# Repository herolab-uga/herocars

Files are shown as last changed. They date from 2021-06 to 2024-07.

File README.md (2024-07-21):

# HeRoCars Project
This repo consists of details and open-sourced codes and materials of the HeRoCars - a Robotics Learning Technology developed at the Heterogeneous Robotics Lab of the University of Georgia. HeRoCars is a simulator-hardware integrative framework consisting of a game-inspired Unity-based Simulator module and a low-cost hardware module of robotized RC cars. 

Go to [Wiki page](https://github.com/herolab-uga/herocars/wiki) for more details.

# Welcome to the HeRoCars Project!
In this research, we focus on innovation in low-cost, open, intuitive learning and  education  methodologies  for  teaching  Robotics,  AI,  and  related  subjects. Here,  we  integrate  the  use  of  games  (e.g.,  Unity simulator  tool  for  testing robotic algorithms) and toys (RC vehicles converted to innovative robot plat-forms) in the proposed project. We first transform (robotize) a commercial RC car into a programmable car capable of sensing its environment through cameras and IR sensors and moving on a race track on its own using a microcomputer unit. Then, we develop a game-inspired Unity-based simulator for the car. Both the real car and the simulator are integrated in terms of the same educational modules that help teach and learn Robotics and AI concepts such as lane following and motor control.

## What will you learn from this project?
This project is jampacked with cool ideas, interesting technologies, and interactive activities for the user to take part in! One major thing you will learn about is AI! AI comes in many shapes and sizes and has a very broad range of possibilities. For this project, we will be discussing a very popular AI that is common in self-driving cars around the world! That AI model is a PID controller or a proportional–integral–derivative controller . A PID controller consist of 3 calculations that are then combined together to give you a smooth decision tree. Ever wonder why your air conditioner doesn't constantly make the temperature way colder the moment the temperature goes ever so slightly below the set temp? The reason is that many of them use a PID controller to help smooth out the temperature pattern and keep the temperature consistent without constantly overshooting the desired temperature. We will break the PID controller into 3 parts and describe what each element does, how it affects decisions, and how this can be applied into an RC car which we will make here shortly. But first, we must learn what an error is!

## Basics of PID and Error
[Click Here](https://github.com/herolab-uga/herocars/wiki/PID-Controller-and-Error) to learn about the PID controller and the concept of Error! You should fully read this before moving on for these two concepts are the main driving ideas behind this project.

## RC Car Hardware Assembly and Software Installation
There are two guides for building the car and installing the software. It is recommended that you start with the hardware portion and then do the software installation. 

[Click Here](https://github.com/herolab-uga/herocars/wiki/Hardware-Assembly-Guide) for the hardware assembly guide.

[Click Here](https://github.com/herolab-uga/herocars/wiki/Software-Assembly-Guide) for the software installation guide.

## RC Car Simulation in Unity Game Environment
[Click Here](https://github.com/herolab-uga/herocars/wiki/Simulator-Instructions) for instructions, information and a link to download our RC car simulator software designed with the Unity game engine!

## RC Car Interface Tool to Control and Test the Hardware Car (Integrated with the Simulation Software)
[Click Here](https://github.com/herolab-uga/herocars/wiki/RC-Car-Interface) for instructions on how to use the Unity-based simulator software to interface and control the actual RC car

## Final Robotized RC Car After Assembly
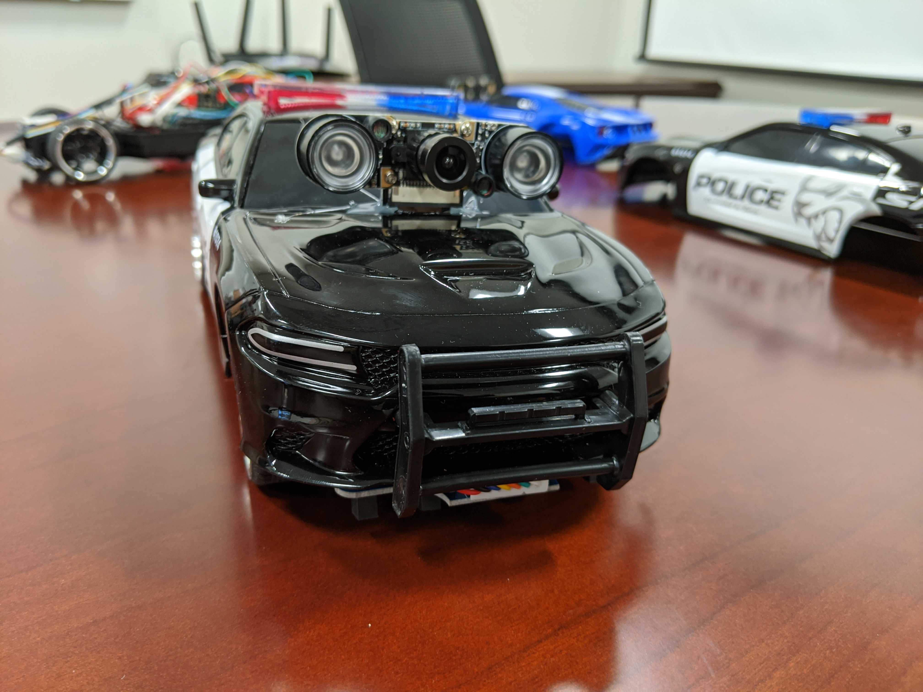
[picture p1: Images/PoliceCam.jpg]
RC Car

## Demo of the Robotized RC Car Driving Around the Track
RC Car Driving Around the Track
## Demo of the Simulator Software
Demo Vid

## Core contributors

* **Anderson Molter** - (https://github.com/andersonmolter1)

* **Sanjay Sarma O.V** - (https://github.com/sanjayovs)

* PI: Prof. Ramviyas Parasuraman - HeRoLab,  UGA - (http://hero.uga.edu)

* Co-PI: Prof. Prashant Doshi - THINC Lab, UGA - (http://thinc.cs.uga.edu)

## Heterogeneous Robotics (HeRoLab)

This project is a part of a Learning Technology Grant (LTG) project at the Heterogeneous Robotics Research Lab (HeRoLab) of the University of Georgia.

Please contact hero at uga . edu for any queries

https://hero.uga.edu/

<p align="center">

</p>

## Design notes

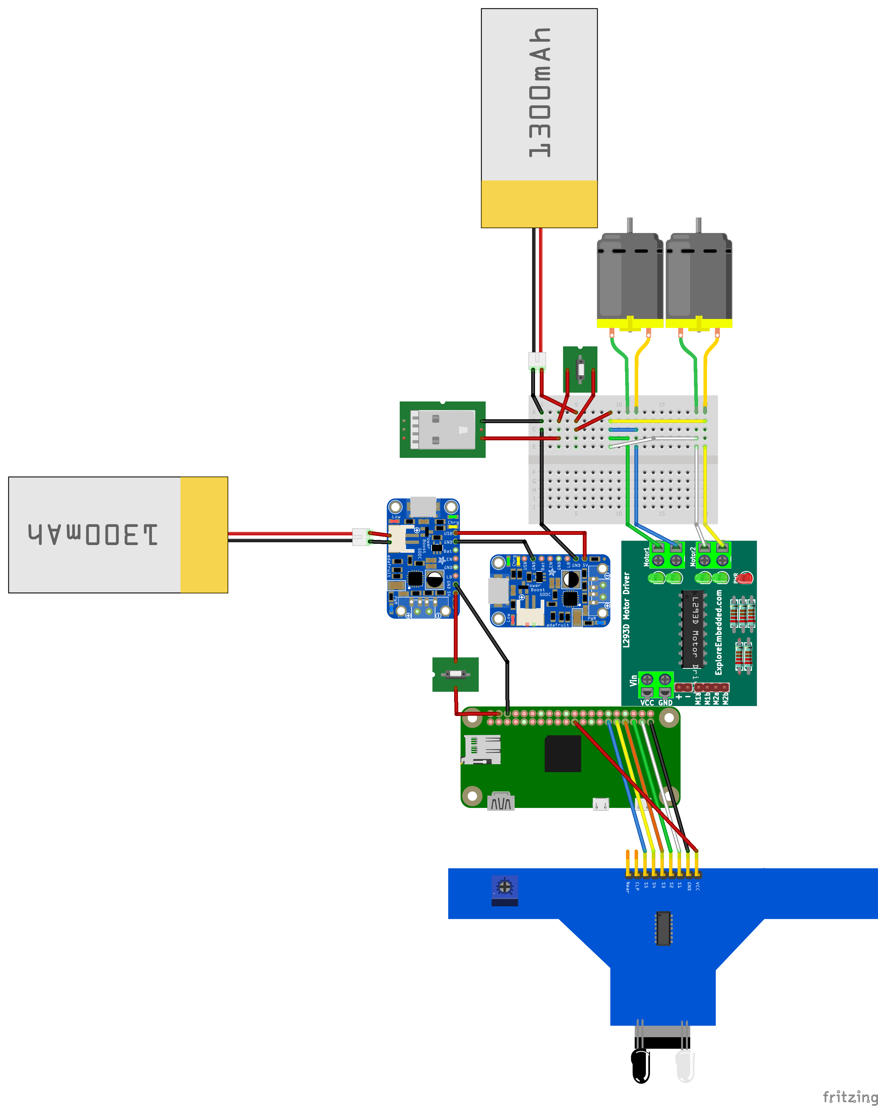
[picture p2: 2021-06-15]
Images/Design_1_bb.png

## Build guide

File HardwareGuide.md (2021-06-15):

# Hardware Assembly Guide
## Bill of Materials
| Component | Price | Quantity | Description | Part Number/SKU | Link to Buy |
| --- | --- | --- |--- | --- | --- |
| SparkFun Autophat | $29.95 | 1 | MotorDriver and IMU sensor | ROB-16328 | [Link to Buy](https://www.sparkfun.com/products/16328)
| Raspberry Pi Zero Wireless WH (Pre-Soldered Header)| $14.95 | 1 | Small computer for internal motor control and user connectivity | 1052 | [Link to Buy](https://www.pishop.us/product/raspberry-pi-zero-wireless-wh-pre-soldered-header/)
| Tracker Sensor Module 5-ch ITR20001/T | $9.99 | 1 | IR sensor array used to track line. Comes with 5 IR sensors pre-soldered.| ITR20001/T | [Link to Buy](https://www.amazon.com/Waveshare-Tracker-Sensor-ITR20001-Infrared/dp/B01MTPEKDC)
| Jada Toys Hyperchargers | $48.20 | 1 | RC Car in which the components will be installed. | 31122 | [Link to Buy](https://www.amazon.com/Jada-Hyperchargers-Chase-Control-Vehicle/dp/B07TYGQDSH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)
| Camera Module for Raspberry PI | $13.99 | 1 | Camera to sit on hood of car and stream video to user. | B07JXZ93SK | [Link to Buy](https://www.amazon.com/Dorhea-Raspberry-Camera-Adjustable-Focus-Infrared/dp/B07JXZ93SK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)
| JDB Ultra-Slim 5V/2.1A 5000mAh Power Bank | $9.99 | 1 | Power bank for all components of car. | 5K01 | [Link to Buy](https://www.amazon.com/gp/product/B07DQG75MZ/ref=ppx_yo_dt_b_search_asin_title?ie=UTF8&psc=1)
| Short USB C Cable | $6.99 | 1 | Cable to connect the Autophat to the battery bank via USB-C to USB-A.| 2724571560050 |  [Link to Buy](https://www.amazon.com/gp/product/B08LL1SVZD/ref=ppx_yo_dt_b_search_asin_title?ie=UTF8&psc=1)

## Hardware
Much work has done to simplify this process of assembling the car itself. But to start this process, you must first have the car. For this project, we are using a Jada R/C Hypercharger RC car. The pack will come with a police car and red race car. Both cars work the same way, however, the police car has a little more space inside so we will start with that one. However, all elements of this tutorial apply to both.

The Fritzing diagram below lays out the electrical diagram the car will follow. If you are confused by an instruction or image, it is HIGHLY recommended to come back to this guide.

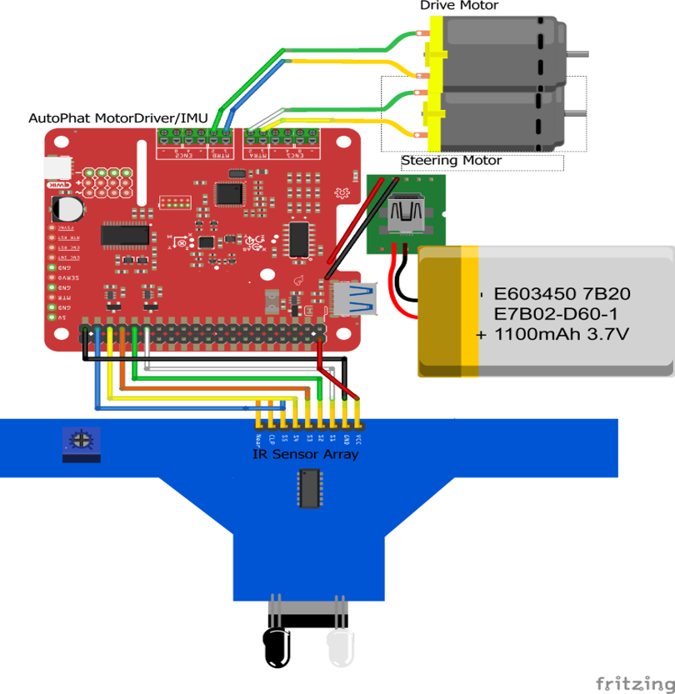
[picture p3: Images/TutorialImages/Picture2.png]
Frit


### Required Tools and Materials
For this project, you need, the car, a Raspberry Pi Zero W, a Sparkfun AutoPhat, GPIO connectors and wires, a 5 IR sensor array, hot glue gun, electrical tape, wire cutters, and a phillips screw driver.  Soldering iron is not required but can help secure connections we will make. 

### Prepare the Car
To prepare the car, we will take 4 screws off so we may take the top of the car off. Save these screws for we will need these later when we put the lid back on.

InitialScrews

Once the lid is off, we will be gaining access to more of the green, blue, yellow, and gray wires that run from the two motors to the internal of the car. If you intend on restoring the intial use of the car, with the remote that comes in the box, you must keep the red wire that comes out of the chimney like hole intact. You can do this by taking the panel in the middle of the car off with its two screws, putting that wire through the side of the car, and screwing that piece back on. 

We need to cut the yellow, gray, green, and blue wires in a way that allows us to extend them and make them into GPIO connectors. I like to cut them fairly close to the middle of the car allowing most of the wire that runs to the two ends of the car to still be intact. 

### Setup Wires
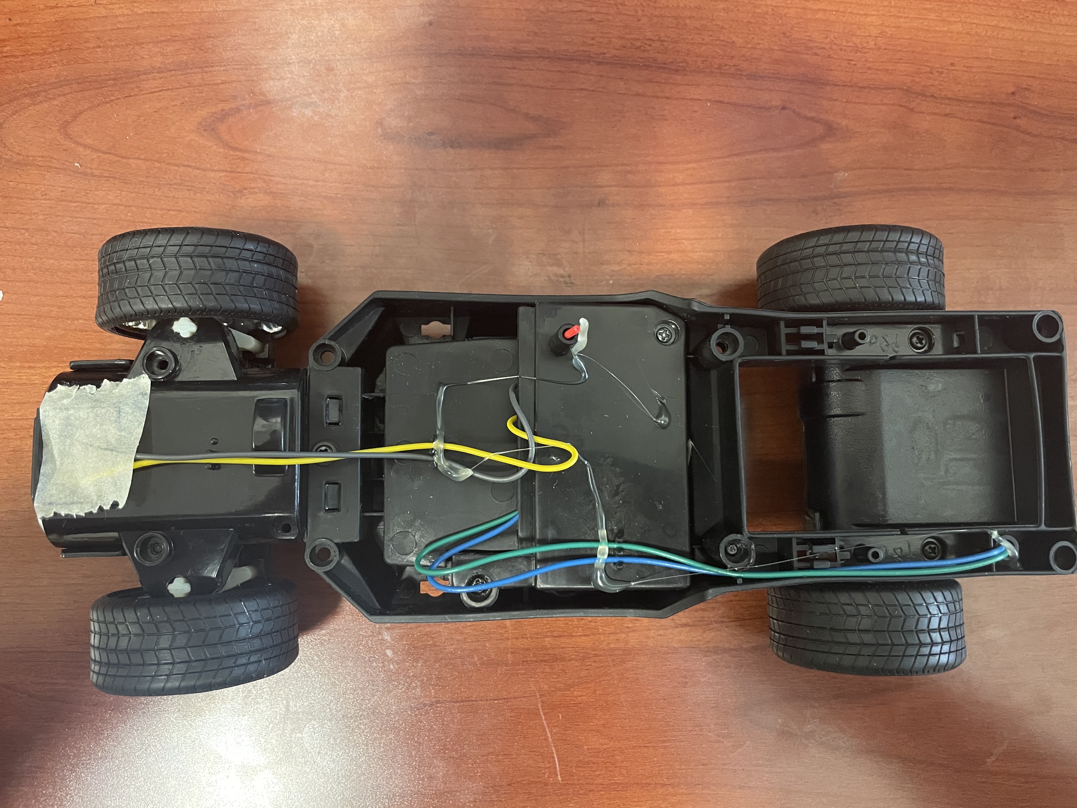
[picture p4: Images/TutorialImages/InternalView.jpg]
GetWires


Once this is completed, we need to make these cables both long enough and able to be inserted into the AutoPhat's Pheonix connector. This can be done in a multitude of ways. You can solder these connectors, connect them via GPIO connectors, or simply twist the tips of wires and electrical tape them together. 

Of course, soldering is the best method of securing a connection but all 3 of them will suffice. These cables need to reach 3/4 down the car indicated in the image below. A fair amount of slack is recommended. 

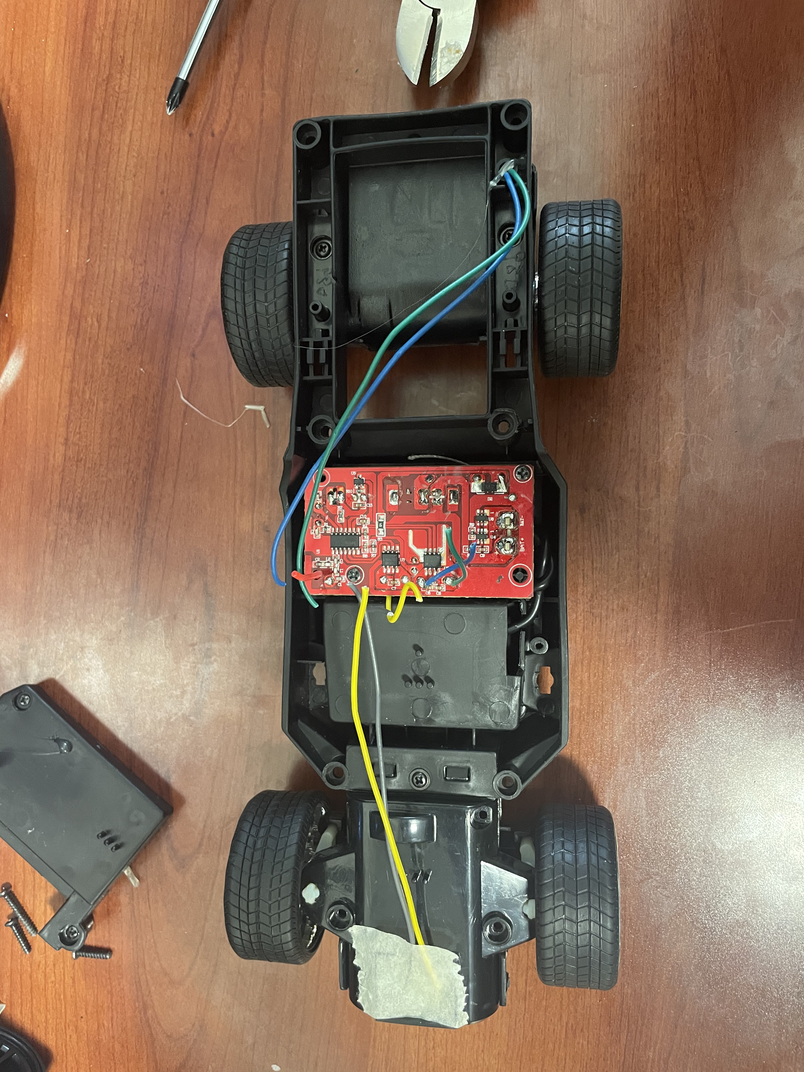
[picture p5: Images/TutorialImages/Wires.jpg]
GPIOWhere?


### Gluing Raspberry Pi Zero W
Now lets tackle the Raspberry Pi. Take your hot glue gun and glue the pi in the same spot I did in the image below. The camera connector, the white strip with a gray strip on one of the ends of the pi, on the edge of the inside body of the car. Position shown below.

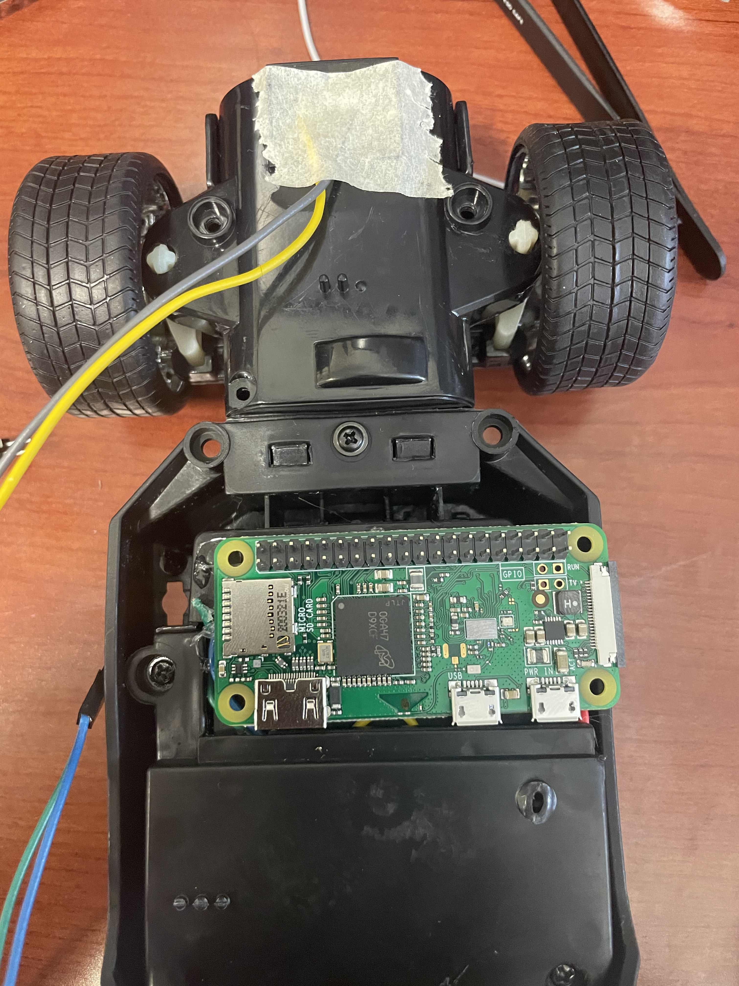
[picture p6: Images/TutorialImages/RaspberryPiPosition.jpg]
RaspberryPiPosition


### Attaching IR Sensor Array
We next need to attach the IR sensor array to the bottom front of the car. The position is shown in the image below. It does not have to be exact but you do need to make sure that the wheels are not able to come in contact with this IR array when the wheels are turning. 

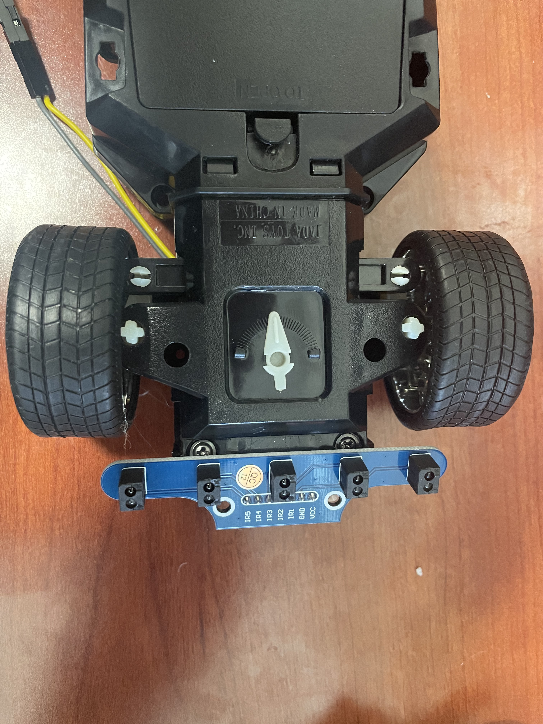
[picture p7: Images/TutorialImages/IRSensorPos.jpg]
IRSensor


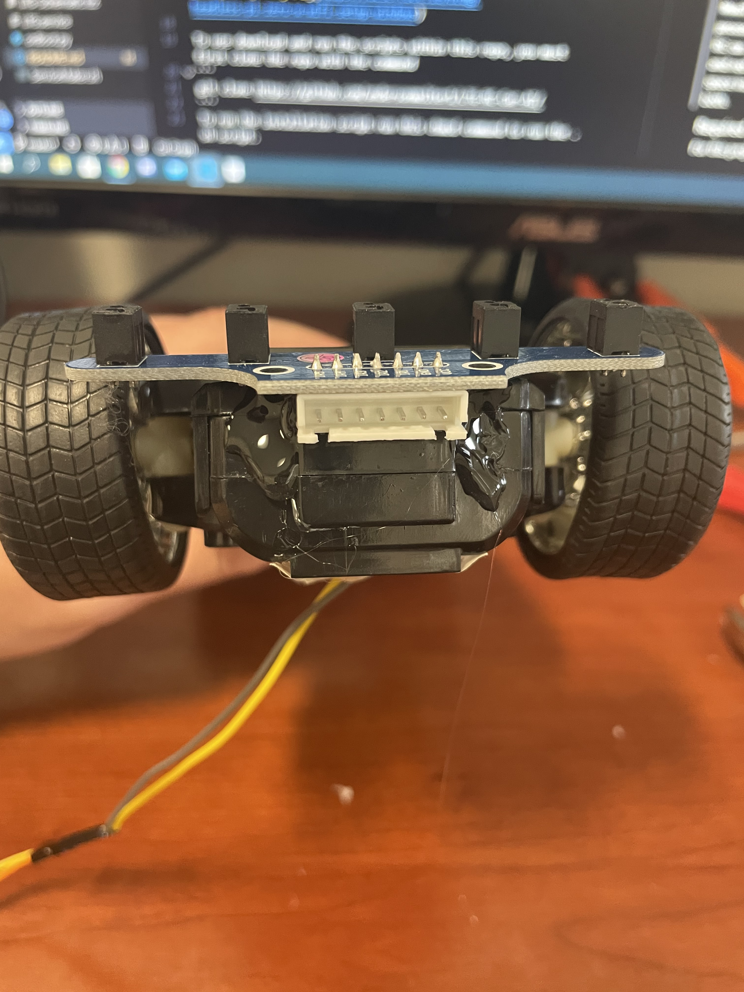
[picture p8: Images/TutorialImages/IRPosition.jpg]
IRSensor2


### AutoPhat Configuration
Next, we are going to put the AutoPhat on the top of the Raspberry Pi. The black bar on the bottom of it connects to the GPIO connectors on the Raspberry Pi. Face it so the green or black phenoix connectors are facing the back of the car. In the image below they are black. 

DO NOT hot glue the AutoPhat to anything. It will stay in place by the friction of the GPIO connectors on the Raspberry Pi. 

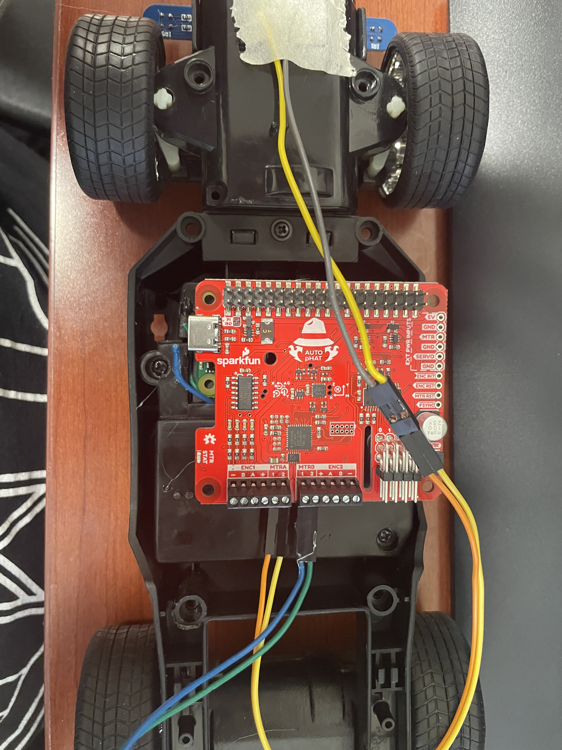
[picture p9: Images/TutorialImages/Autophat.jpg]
AutoPhat


### Pheonix Connectors
Then connect the gray and yellow wires to MTRA1 and MTRA2 respectively. Then connect the blue and green wires to MTRB1 and MTRB2 respectively. To connect the wires to the Pheonix connectors, simply unscrew the top flathead screw until the wire is able to enter in the connector and then tighten it down.

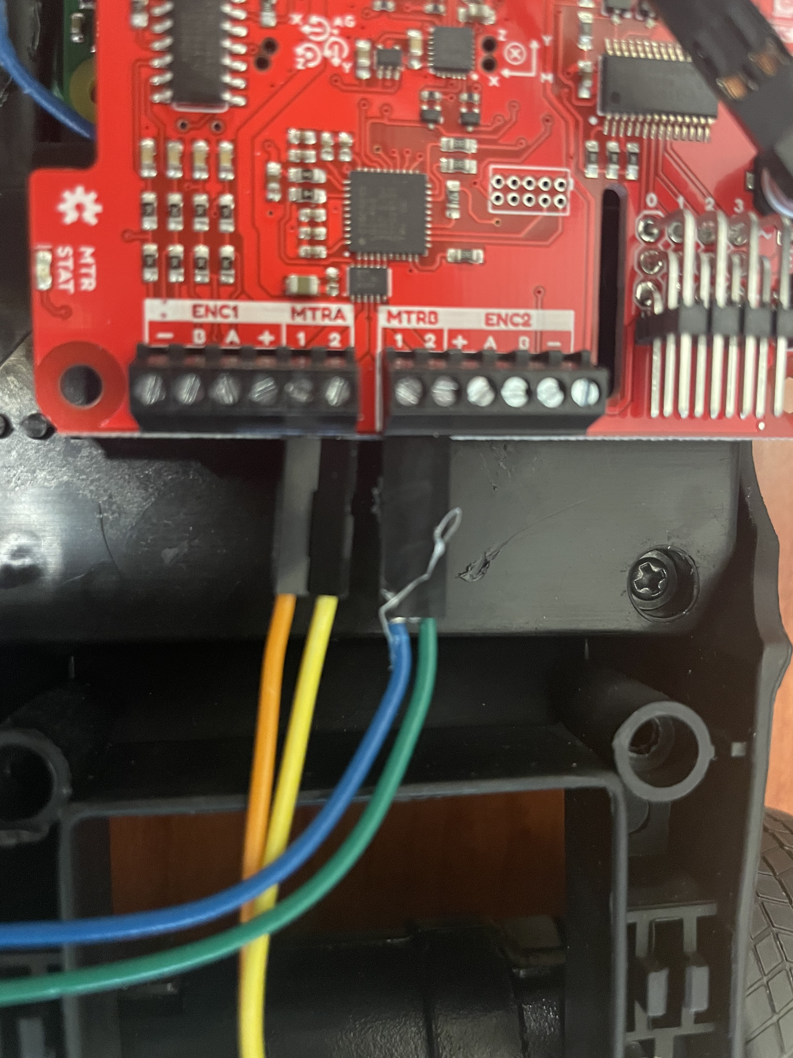
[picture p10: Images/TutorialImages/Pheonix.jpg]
Pheonix


### Connecting GPIO Wires to Raspberry PI
Now connect the IR sensor connector to the IR sensor and run the wires from the front of the car to the Sparkfun Autophat and connect them to the GPIO pins in the electrical diagram above. 

ORDER MATTERS!!!

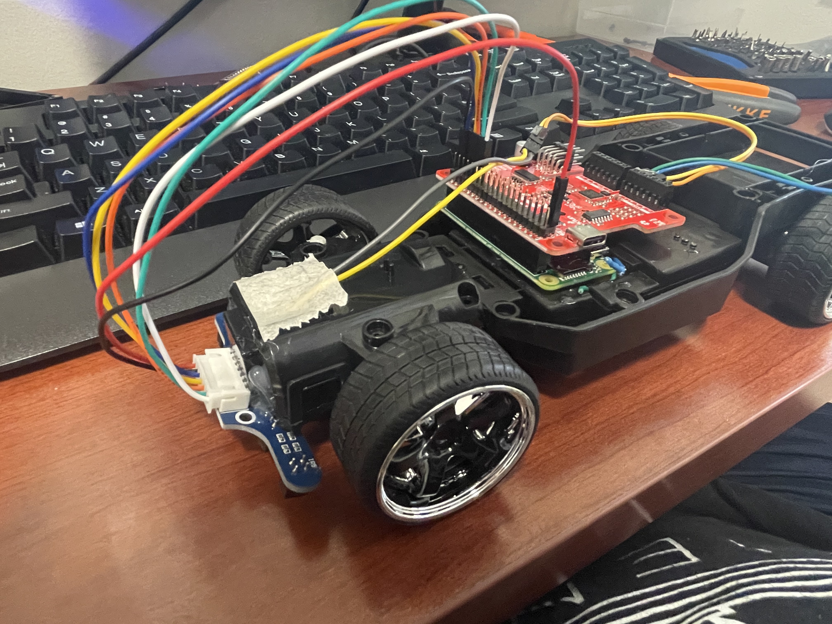
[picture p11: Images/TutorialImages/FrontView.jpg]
IRSensorConnect


### Outer Body
That is all that needs to be done to the internal of the car. Now get the lid back infront of you along with your hot glue gun. Below are images on how to route the camera wire and the power cable 
which will run from the back of the car. The car is powered by a battery bank which is hot glued to the back of the car. You will run the power cable in between the panels of the outer lid of the car.

This is where you can be creative for aslong as these connectors can make it from camera to camera slot on the Pi, and from the battery bank to the AutoPhats USB C connector, you can connect it how you would like. 

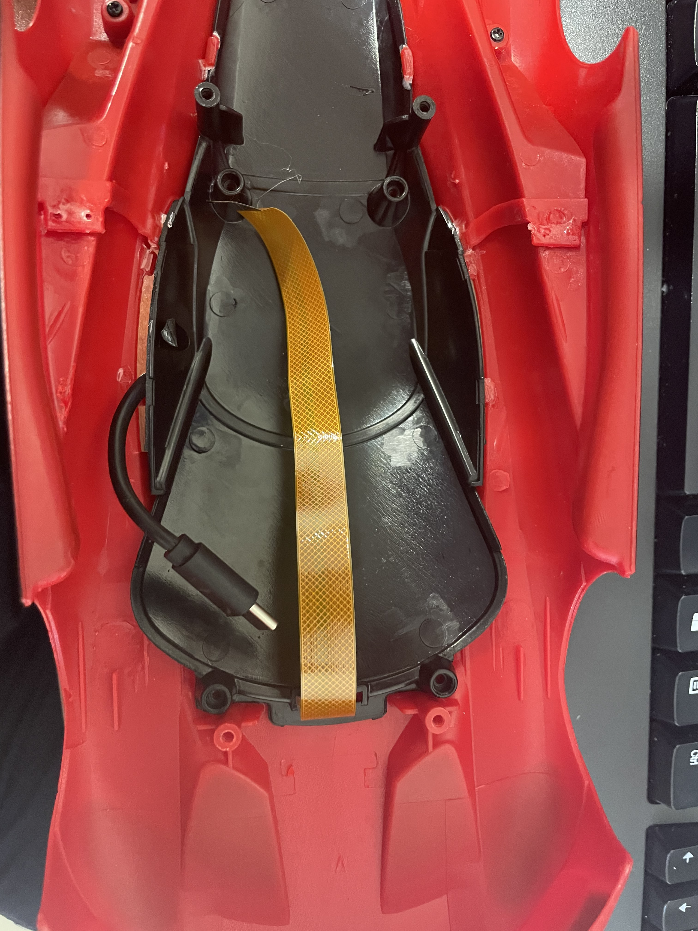
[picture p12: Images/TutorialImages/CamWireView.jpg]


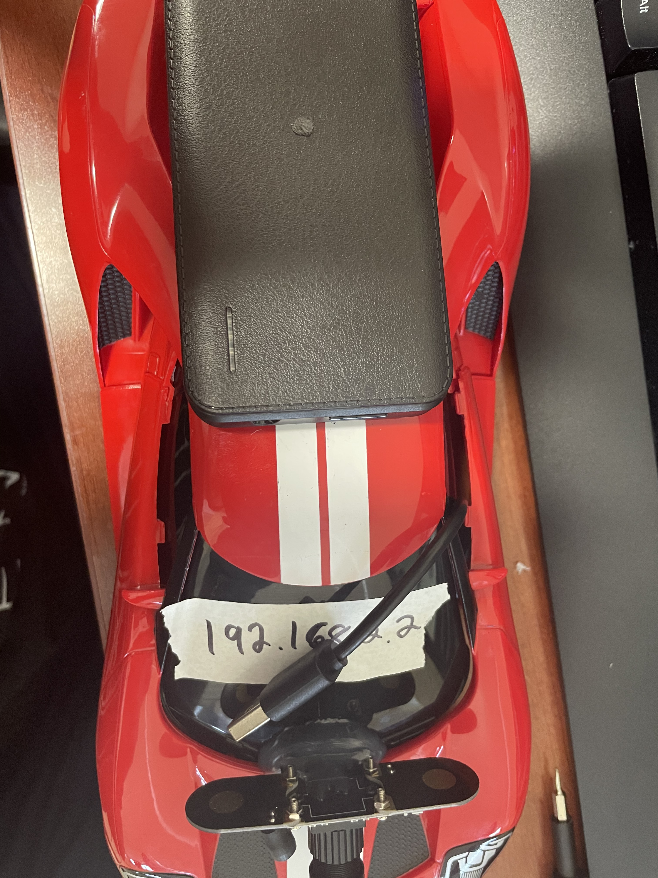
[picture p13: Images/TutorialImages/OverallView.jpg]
ImagesOfOuterCar2


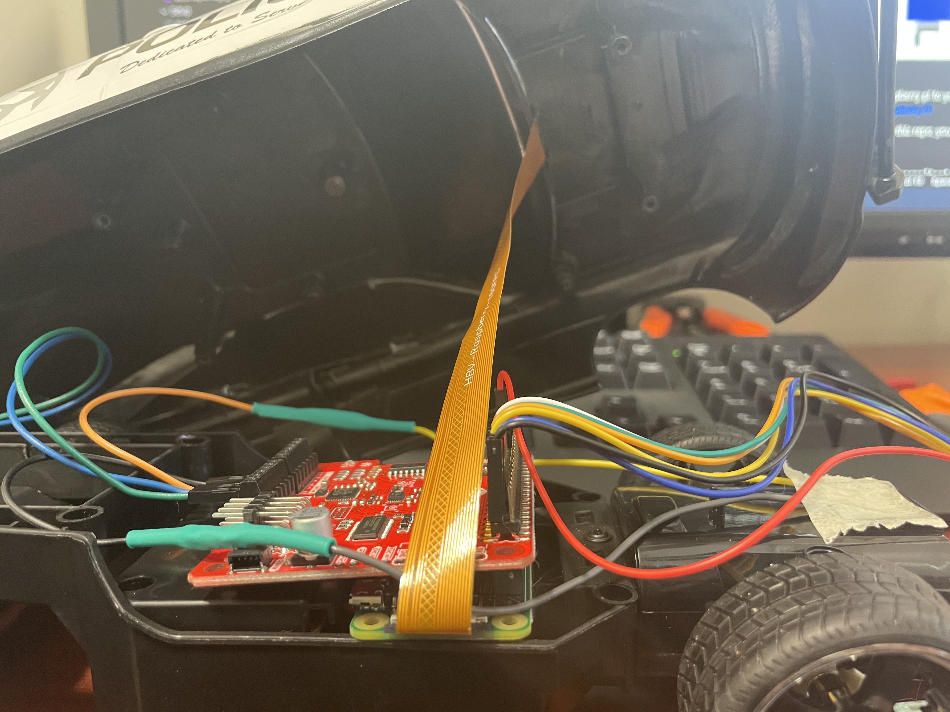
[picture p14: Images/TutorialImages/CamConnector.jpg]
ImagesOfOuterCar3


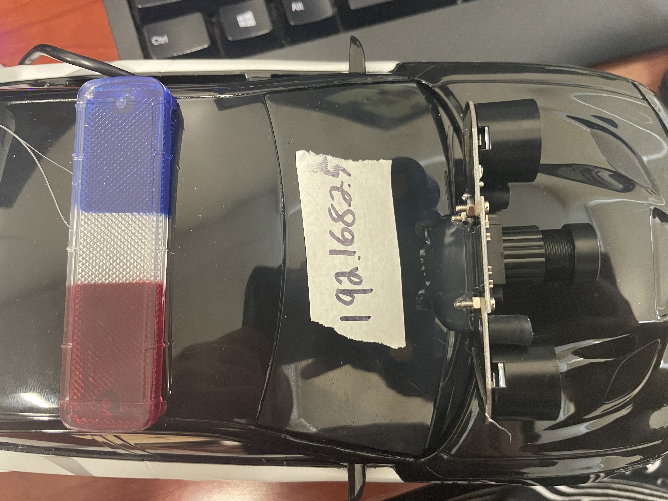
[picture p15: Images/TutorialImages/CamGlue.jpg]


Once you connect those two wires to the internals, you just need the micro sd card with Raspbian to go into the Pi within the car. However, more setup is required to be able to connect to the Raspberry Pi. Below is a complete comprehensive guide to setting the software side of this project up. 

But for now, assuming you have properly setup the micro-sd card, you can insert it into the Pi, and connect the power cable to the battery bank. You will see green flashing lights if the Raspberry Pi is properly booting up. Once you confirmed this, you can put the 4 screws back connecting the lid to the internal car.

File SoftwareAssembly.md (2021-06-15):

# Software Assembly Guide

## Imaging Micro SD Card

Download the *.img file to your local folder on your laptop

Use an imaging tool such as Balena Etcher https://www.balena.io/etcher/ to write the .img file to your SD card by selecting the image and your micro sd card slot. Then select flash!

Once the image is flashed, take out the micro SD card and insert it back into your computer. 

Open up the notepad and hit space once. Then save this file and name the file ssh and click all files in the file type selector. 

Open up notepad again and type in the text below.
```
country=US
ctrl_interface=DIR=/var/run/wpa_supplicant GROUP=netdev
update_config=1

network={
    ssid="herolabcar"
    psk="herolabcar"
}
network={
    ssid="Name of Network"
    psk="Password of Network"
}
```
If your network is not listed, add in your network name and password in the open option. Once you have named this file wpa_supplicant.conf and selected the All Files option, you may save this file. 

Drag and drop these files onto your raspberry pi boot drive.

## Creating Your Own Hotspot from Your Windows Laptop

Select the Start  button, then select Settings  > Network & Internet > Mobile hotspot.

For Share my Internet connection from, choose the Internet connection you want to share.

Select Edit > enter a new network name and password > Save.

Turn on Share my Internet connection with other devices.

To connect on the other device, go to the Wi-Fi settings on that device, find your network name, select it, enter the password, and then connect.

## Set Static IP Address
If you used the image provided, the car will not have a static IP address.  If you would like to set one, that can be done with the command 
```
sudo /home/pi/LTG-RC-Car/SetStaticIP.sh
```
It will prompt you to provide a static IP, use the range 192.168.0.0 – 192.168.255.255, and then type in your routers IP address or the default gateway. This will likely be 192.168.1.1 or 192.168.0.1.

If you are using the installation script, you do not need to independently set the static IP. It will be apart of the installation script.

## Installing the Software Manually

If you would like to install and setup the software manually, you may use the scripts within this repo for manual installation. For instructions on how to connect the raspberry pi to your network and install Stock Raspbian Buster, follow these instructions, [Setup Raspberry PI](https://desertbot.io/blog/headless-pi-zero-w-wifi-setup-windows) Now that you have installed raspbian and have connected to the Raspberry Pi through your ssh client, you need to run two commands before we start our installation scripts.
```
sudo apt-get update && sudo apt-get upgrade -y && sudo apt-get install git -y
```
To use download and run the scripts within this repo, you must first clone the repo with the command
```
git clone https://github.com/andersonmolter1/LTG-RC-Car/
```
The script we will be running below will prompt ask for what you would like the static ip of the raspberry pi to be, enter it and hit enter and allow the installation to proceed. The command to run this script is below.
```
sudo ./LTG-RC-Car/Setup/Install.sh
```
A prompt will open up with different options for the camera setup after a little while, just hit enter and let the installation proceed.

Once it is over, you will be prompted with a decision if you want to Auto-Start the cam stream when the pi is turned on, hit enter at this option selecting Yes.

## How to run? 
Guess what! The script is already running if you flashed the image to your micro sd or used the installation script. All operations that the car requires are now running as a service, which means they run at boot of the pi. If the car cannot be connected to, first check to see if the service named LTG is running with the command below.
```
sudo systemctl status LTG.service
```
If this comes back that is not running, you can re-create the service by running the ServiceMaker.sh script and this will re-create the service. If that fails as well, you can manually run the script for car operations with the command below.
```
python3 LTG-RC-Car\AI_Driver\main.py
```

## Authors

* **Anderson Molter** - (https://github.com/andersonmolter1)
* **Sanjay Sarma** - (https://github.com/sanjayovs)
* PI: Prof. Ramviyas Parasuraman - HeRoLab UGA - (http://hero.uga.edu)

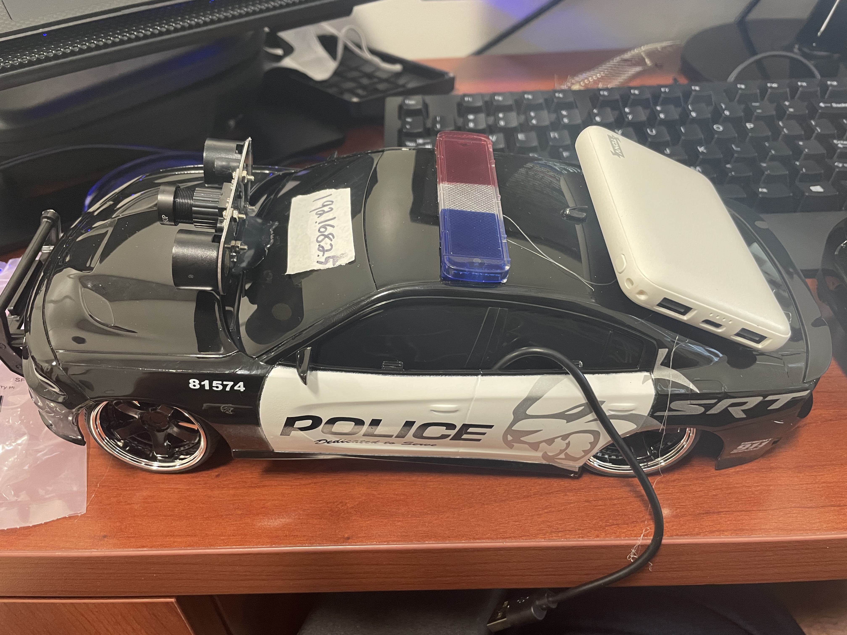
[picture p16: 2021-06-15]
Images/TutorialImages/OuterView.jpg

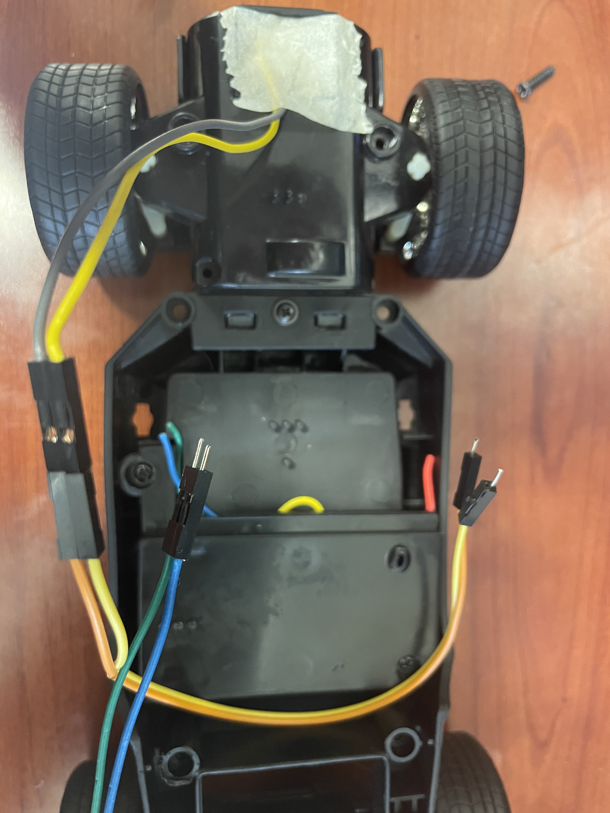
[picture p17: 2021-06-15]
Images/TutorialImages/GPIOWires.jpg

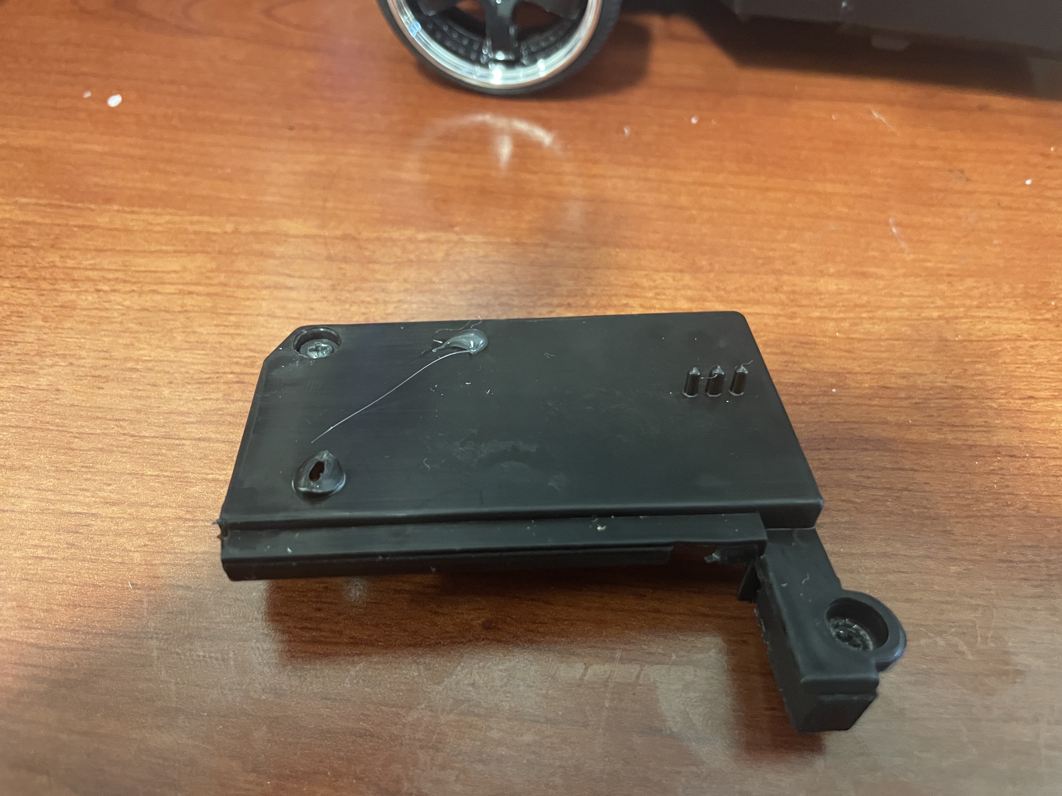
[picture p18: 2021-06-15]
Images/TutorialImages/InternalProtector.jpg

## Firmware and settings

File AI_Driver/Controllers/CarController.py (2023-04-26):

from socketserver import ThreadingUnixDatagramServer
import cv2
import time
import threading
import queue
import RPi.GPIO as GPIO
from AI_Driver.AutoPhat.AutoPhatMD import AutoPhatMD

class CarController:

    def __init__(self) -> None:
        # Initialize the car

        # Autohat Object
        self._motor_driver = AutoPhatMD()

        self._min_speed = 0
        self._max_speed = 150
        self._line_color = "White" # 1: white, 0: black

        self._last_velo_time = 0 # last time the car was commanded to drive in manual mode
        self._last_steer_time = 0 # last time the car was commanded steer in manual mode

        self._p = 43       # Proportion value
        self._i = 1        # Integral Step value
        self._d = 13       # Derivative Step Value
        self._error = 0      # amount of _error on the line the car is experiencing
        self._prev_error = 0  # _error of last calculation used for Derivative calc
        self._straight = 1     # 1: _straight, 0: not _straight

        self._control_type = "Auton" # 0:Manual, 1:Auton

        self._PV = 0  # sum of all values errors that the car has experienced

        self._car_speed = 0 # speed of the car

        self._camera_queue = queue.Queue(maxsize=1)

        GPIO.setmode(GPIO.BOARD)
        GPIO.setup(29, GPIO.IN)  # RR IR Sensor
        GPIO.setup(31, GPIO.IN)  # RM IR Sensor
        GPIO.setup(33, GPIO.IN)  # MM IR Sensor
        GPIO.setup(35, GPIO.IN)  # LM IR Sensor
        GPIO.setup(37, GPIO.IN)  # LL IR Sensor

        self.thread = threading.Thread(target=self.read_camera, args=(), daemon=True)
        self.thread.start()

        # Create update thread
        update_thread = threading.Thread(target=self.auton_control_update,args=(),daemon=True)
        update_thread.start()

        # # Create stop thread
        stop_thread = threading.Thread(target=self.car_auto_stop,args=(),daemon=True)
        stop_thread.start()

    # Create getter and setter methods for the last_time variable
    @property
    def last_velo_time(self):
        return self.last_velo_time

    @last_velo_time.setter
    def last_velo_time(self, value):
        self._last_velo_time = value

    # Create getter and setter methods for the _last_steer_time variable
    @property
    def last_steer_time(self):
        return self._last_steer_time

    @last_steer_time.setter
    def last_steer_time(self, value):
        self._last_steer_time = value

    # Create getter and setter methods for the car's _p, _i, and _d
    @property
    def p(self):
        return self._p

    @p.setter
    def p(self, value):
        self._p = value

    @property
    def i(self):
        return self._i

    @i.setter
    def i(self, value):
        self._i = value

    @property
    def d(self):
        return self._d

    @d.setter
    def d(self, value):
        self._d = value

    # Create getter and setter methods for the car's _car_speed
    @property
    def car_speed(self):
        return self._car_speed

    @car_speed.setter
    def car_speed(self, value):
        self._car_speed = value

    # Create getter and setter methods for the car's _line_color
    @property
    def line_color(self):
        return self._line_color

    @line_color.setter
    def line_color(self, value):
        self._line_color = value

    # Create getter and setter methods for the car's _error
    @property
    def error(self):
        return self._error

    @error.setter
    def error(self, value):
        self._error = value

    # Create getter and setter methods for the car's _min_speed
    @property
    def min_speed(self):
        return self._min_speed

    @min_speed.setter
    def min_speed(self, value):
        self._min_speed = value
    
    # Create getter and setter methods for the car's _max_speed
    @property
    def max_speed(self):
        return self._max_speed
    
    @max_speed.setter
    def max_speed(self, value):
        self._max_speed = value

    # Create getter and setter methods for the car's _control_type
    @property
    def control_type(self):
        return self._control_type
    
    @control_type.setter
    def control_type(self, value):
        self._control_type = value

    # Create getter for the camera frame
    @property
    def camera_frame(self):
        return self._camera_frame

    # Create getter for the _straight variable
    @property
    def straight(self):
        return self._straight 

    # Create setter for the _straight variable
    @straight.setter
    def straight(self, value):
        self._straight = value

    # Gets the speed proportional to the _error
    def calculate_speed(self):
        self._car_speed = min(abs(int(abs(self._error) * (self._max_speed /4))) + self._min_speed, self._max_speed)
        return self._car_speed

    # Reads the frame from the camera
    def read_camera(self):
        # Create the video capture object
        cap = cv2.VideoCapture(0)

        # Loop until the camera is open
        while not cap.isOpened():
            pass

        # Loop until the camera is open
        while True:
            # Read the frame
            success,frame = cap.read()

            if not success:
                continue

            if self._camera_queue.empty():
                self._camera_queue.put(frame)
                

    def get_frame(self):
        while True:
            frame = self._camera_queue.get()
            ret,buffer = cv2.imencode('.jpg',frame)
            frame = buffer.tobytes()
            yield (b'--frame\r\n'
                b'Content-Type: image/jpeg\r\n\r\n' + frame + b'\r\n')  # concat frame one by one and show result

    # Gets the state of the car's line
    def get_line_state(self):
        # Get the states of the IR sensors
        line_state = [GPIO.input(37), GPIO.input(35), GPIO.input(33), GPIO.input(31), GPIO.input(29)]

        # If the line is set to white return the list
        if self._line_color == "White":
            return line_state
        # If the line is set to black return the list with the opposite values
        else:
            return [not x for x in line_state]

    def calculate_error(self):

        self.prevError = self._error

        # Combine IR sensors into _error value

        # Get the states of the IR sensors
        LL,LM,MM,RM,RR = self.get_line_state()
        try:
            self._error = (4*RR + 2*RM + 0 + -2*LM + -4*LL) / (RR + RM + MM + LM + LL)
        except ZeroDivisionError:
            print("not on line")
        if abs(self._error) < 4:
            self._PV += -.0001 * self._error

        self._PV = max(self._PV,-10)
        self._PV = min(self._PV,10)
            
        return self._error
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

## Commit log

2021-06-15 Transition to herocars repo
    [LTG-Schematic.fzz]
2021-06-16 Changed at zero power
2022-07-02 added getter for ir sensor state
2022-07-02 added socket control
2022-07-02 added sleep to autostop thread
2022-07-02 removed print statment
2022-07-02 socket test
2022-07-03 print statments for debugging
2022-07-03 added method to force socket bind
2022-07-03 catching socket clase and restarting program
2022-07-03 stopped socket close
2022-07-05 adding camera capture
2022-07-07 reenabled threads
2022-07-07 removed print statments
2022-07-08 enter also means center steering
2022-07-08 testing stop and center steering with keyup
2022-07-28 adding pid
2022-07-28 testing PID route
2022-07-28 print value
2022-07-28 removed duplicate PID functions
2022-07-28 pid vals
2022-07-28 printing request
2022-07-28 print request.data
2022-08-03 print dictionary
2022-08-03 added timer functionality, does not interact with python at all
2022-08-03 added camera image (testing on trident)
2022-08-03 continuously get camera
2022-08-04 control mode and line type buttons working
